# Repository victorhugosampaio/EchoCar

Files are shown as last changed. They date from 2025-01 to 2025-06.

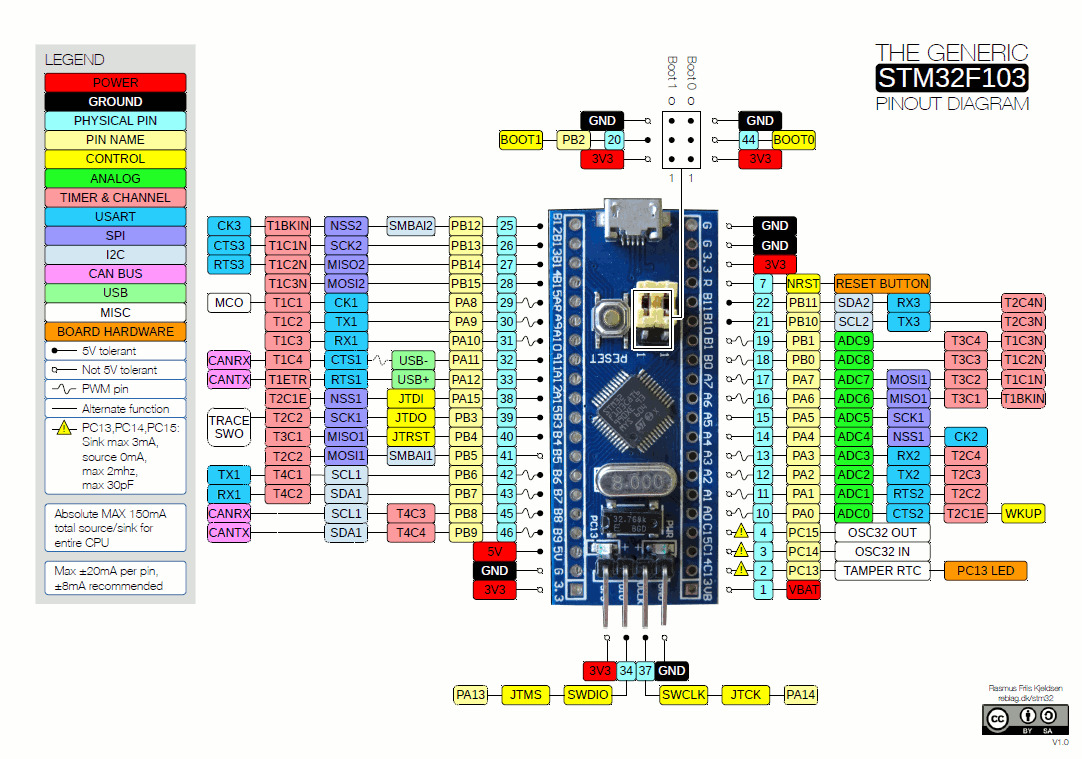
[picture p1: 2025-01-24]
images/Bluepill pinout.jpg

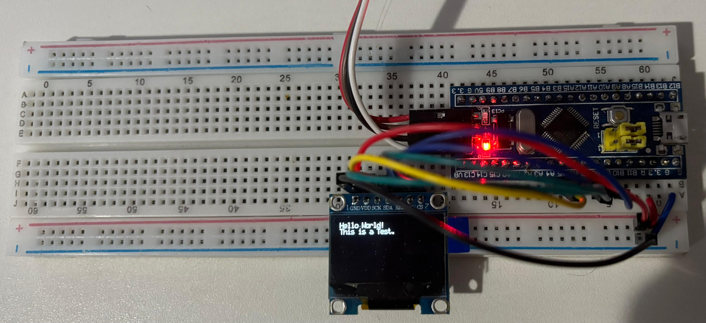
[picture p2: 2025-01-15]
images/display-test.jpg

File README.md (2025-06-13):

# EchoCar

Hi there, my name is Victor. I'm a ~~undergraduate~~ graduated computer engineer, currently working as a firmware trainee engineer. The EchoCar is my final paper project for college.

I used two microcontrollers: a Bluepill (STM32F103C8T6) to control the hardware itself and an Arduino Nano 33 BLE Sense to run the MFCC algorithm and the AI model. I chose to use Zephyr as the RTOS to operate the system. To create and train the AI model and deploy it to the Arduino Nano microcontroller, I used Edge Impulse. I also used it to edit some audio data to fit within the 1-second window for training the model.

I used the Pete Warden voice dataset as the AI databse. The files used in this project can be accessed [here](https://drive.google.com/file/d/17HAxpKHDkPuj7wIeOMZ8yrCH6MHIF1b3/view?usp=sharing).

## Getting Started

Follow these instructions to set up and run the EchoCar project.

### Prerequisites

The project is divided into firmware and hardware.

For the hardware, check the project BOM for the required components.

```
STM32F103C8T6 microcontroller  
Arduino Nano 33 BLE Sense  
EchoCar's PCB  
2x 18650 batteries  
BOM components  
```

For the firmware, install the Zephyr RTOS and the Arduino IDE. You can follow the instructions on the Zephyr Getting Started page to install it on your machine and download the Arduino IDE from their website.

### Installing

After installing Zephyr, flash the firmware onto the STM32F103 using a flasher device such as the ST-Link v2.

First, build the project using:

```
west build -p
```

Then, flash it using:

```
west flash
```

For the Arduino firmware, install the EchoCar_inferencing.rar library in the Arduino IDE, then flash the .ino file to the Arduino Nano microcontroller.

## Built With

* [Zephyr RTOS](https://www.zephyrproject.org/) - The RTOS used.  
* [Edge Impulse](https://edgeimpulse.com/) - Used for AI model development.  
* [KiCad](https://www.kicad.org/) - Used to design the PCB.
* [Pete Warden Dataset](https://arxiv.org/pdf/1804.03209) - AI Dataset.

## Author

* **Victor Hugo Sampaio**

## Video
YouTube [link](https://youtu.be/iiWRqvPNBO4).

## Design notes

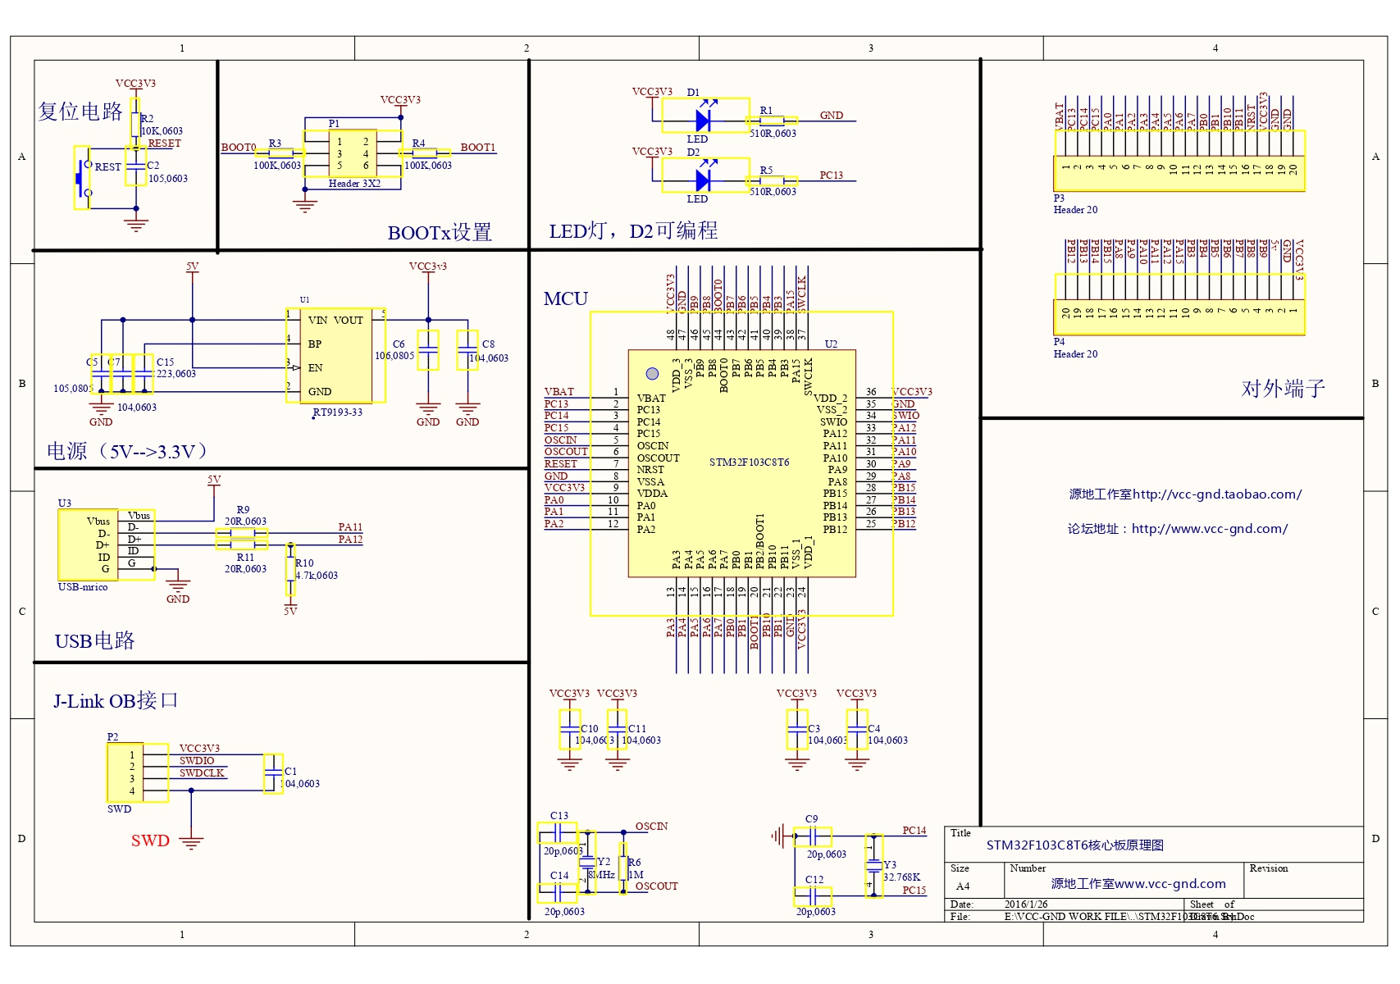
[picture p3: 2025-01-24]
images/Bluepill Schematic.jpg

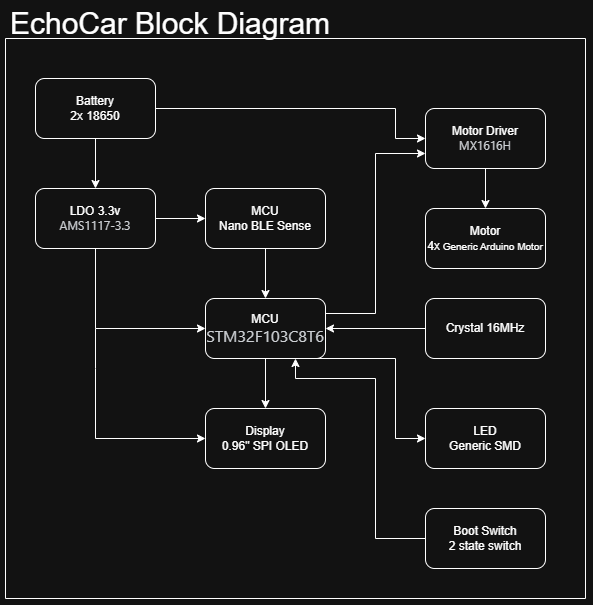
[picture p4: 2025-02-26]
images/EchoCar_Block_Diagram.png

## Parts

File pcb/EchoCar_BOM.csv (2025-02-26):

Reference | Value | Link | Footprint | Qty
C1 | 10u | https://www.lcsc.com/product-detail/Multilayer-Ceramic-Capacitors-MLCC-SMD-SMT_Murata-Electronics-GRM21BR61H106KE43L_C440198.html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 | Capacitor_SMD:C_0805_2012Metric | 1
C2,C3,C4,C5,C6,C7 | 100n | https://www.lcsc.com/product-detail/Multilayer-Ceramic-Capacitors-MLCC-SMD-SMT_TDK-C1005X7R1H104KT000F_C361198.html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 | Capacitor_SMD:C_0402_1005Metric | 6
C8,C9 | 10p | https://www.lcsc.com/product-detail/Multilayer-Ceramic-Capacitors-MLCC-SMD-SMT_TDK-CGA2B2NP01H100DT0Y0F_C694492.html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 | Capacitor_SMD:C_0402_1005Metric | 2
C10,C11 | 22u | https://www.lcsc.com/product-detail/Multilayer-Ceramic-Capacitors-MLCC-SMD-SMT_Samsung-Electro-Mechanics-CL21A226MAQNNNE_C45783.html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 | Capacitor_SMD:C_0805_2012Metric | 2
C12,C13 | 47u 16V | https://www.lcsc.com/product-detail/Aluminum-Electrolytic-Capacitors-SMD_AISHI-Aihua-Group-EMK1CM470E61D00R_C5289725.html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 | Capacitor_SMD:CP_Elec_5x5.3 | 2
D1 | PWR_ON | https://www.lcsc.com/product-detail/LED-Indication-Discrete_Foshan-NationStar-Optoelectronics-NCD0603W3_C158100.html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 | LED_SMD:LED_0603_1608Metric | 1
D2 | BZV55B5V1 | https://www.lcsc.com/product-detail/Zener-Diodes_EIC-Semicon-BZV55B5V1_C2978889.html?s_z=n_BZV55B5V1 | Diode_SMD:D_MiniMELF | 1
J1 | SW | x | Connector_PinHeader_2.54mm:PinHeader_1x04_P2.54mm_Vertical | 1
J2 | Display_Con | x | Connector_PinSocket_1.00mm:PinSocket_1x07_P2.54mm_Vertical | 1
J3 | Arduino_con | x | Connector_PinHeader_2.54mm:PinHeader_1x03_P2.54mm_Vertical | 1
R1 | 10k | https://www.lcsc.com/product-detail/Chip-Resistor-Surface-Mount_Vishay-Intertech-RCS040210K0FKED_C3020235.html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 | Resistor_SMD:R_0402_1005Metric | 1
R2 | 1k | https://www.lcsc.com/product-detail/Chip-Resistor-Surface-Mount_UNI-ROYAL-Uniroyal-Elec-CQ02WGJ0102TCE_C2770748.html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 | Resistor_SMD:R_0402_1005Metric | 1
R3 | 220 | https://www.lcsc.com/product-detail/Chip-Resistor-Surface-Mount_RALEC-RTT022200FTH_C102889.html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 | Resistor_SMD:R_0402_1005Metric | 1
SW1 | SW_SPDT | https://www.lcsc.com/product-detail/Slide-Switches_XKB-Connection-SK12D07L3B_C480339.html?s_z=n_SW%20SPDT | Button_Switch_THT:SW_E-Switch_EG1224_SPDT_Angled | 1
U1 | STM32F103C8T6 | https://www.lcsc.com/product-detail/Microcontrollers-MCU-MPU-SOC_STMicroelectronics-STM32F103C8T6_C8734.html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 | Package_QFP:LQFP-48_7x7mm_P0.5mm | 1
U2 | AMS1117-3.3 | https://www.lcsc.com/product-detail/Voltage-Regulators-Linear-Low-Drop-Out-LDO-Regulators_UMW-Youtai-Semiconductor-Co-Ltd-AMS1117-3-3_C347222.html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 | Package_TO_SOT_SMD:SOT-223-3_TabPin2 | 1
U3 | MX1616H | https://www.lcsc.com/product-detail/Brushed-DC-Motor-Drivers_Mixic-MX1616H_C5119044.html?s_z=n_MX1616H | MX1616H_SMD:MX1616H | 1
Y1 | 16MHz | https://www.lcsc.com/product-detail/Crystals_Shenzhen-SCTF-Elec-SX3B16-000F0910F30_C2901667.html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 | Crystal:Crystal_SMD_3225-4Pin_3.2x2.5mm | 1

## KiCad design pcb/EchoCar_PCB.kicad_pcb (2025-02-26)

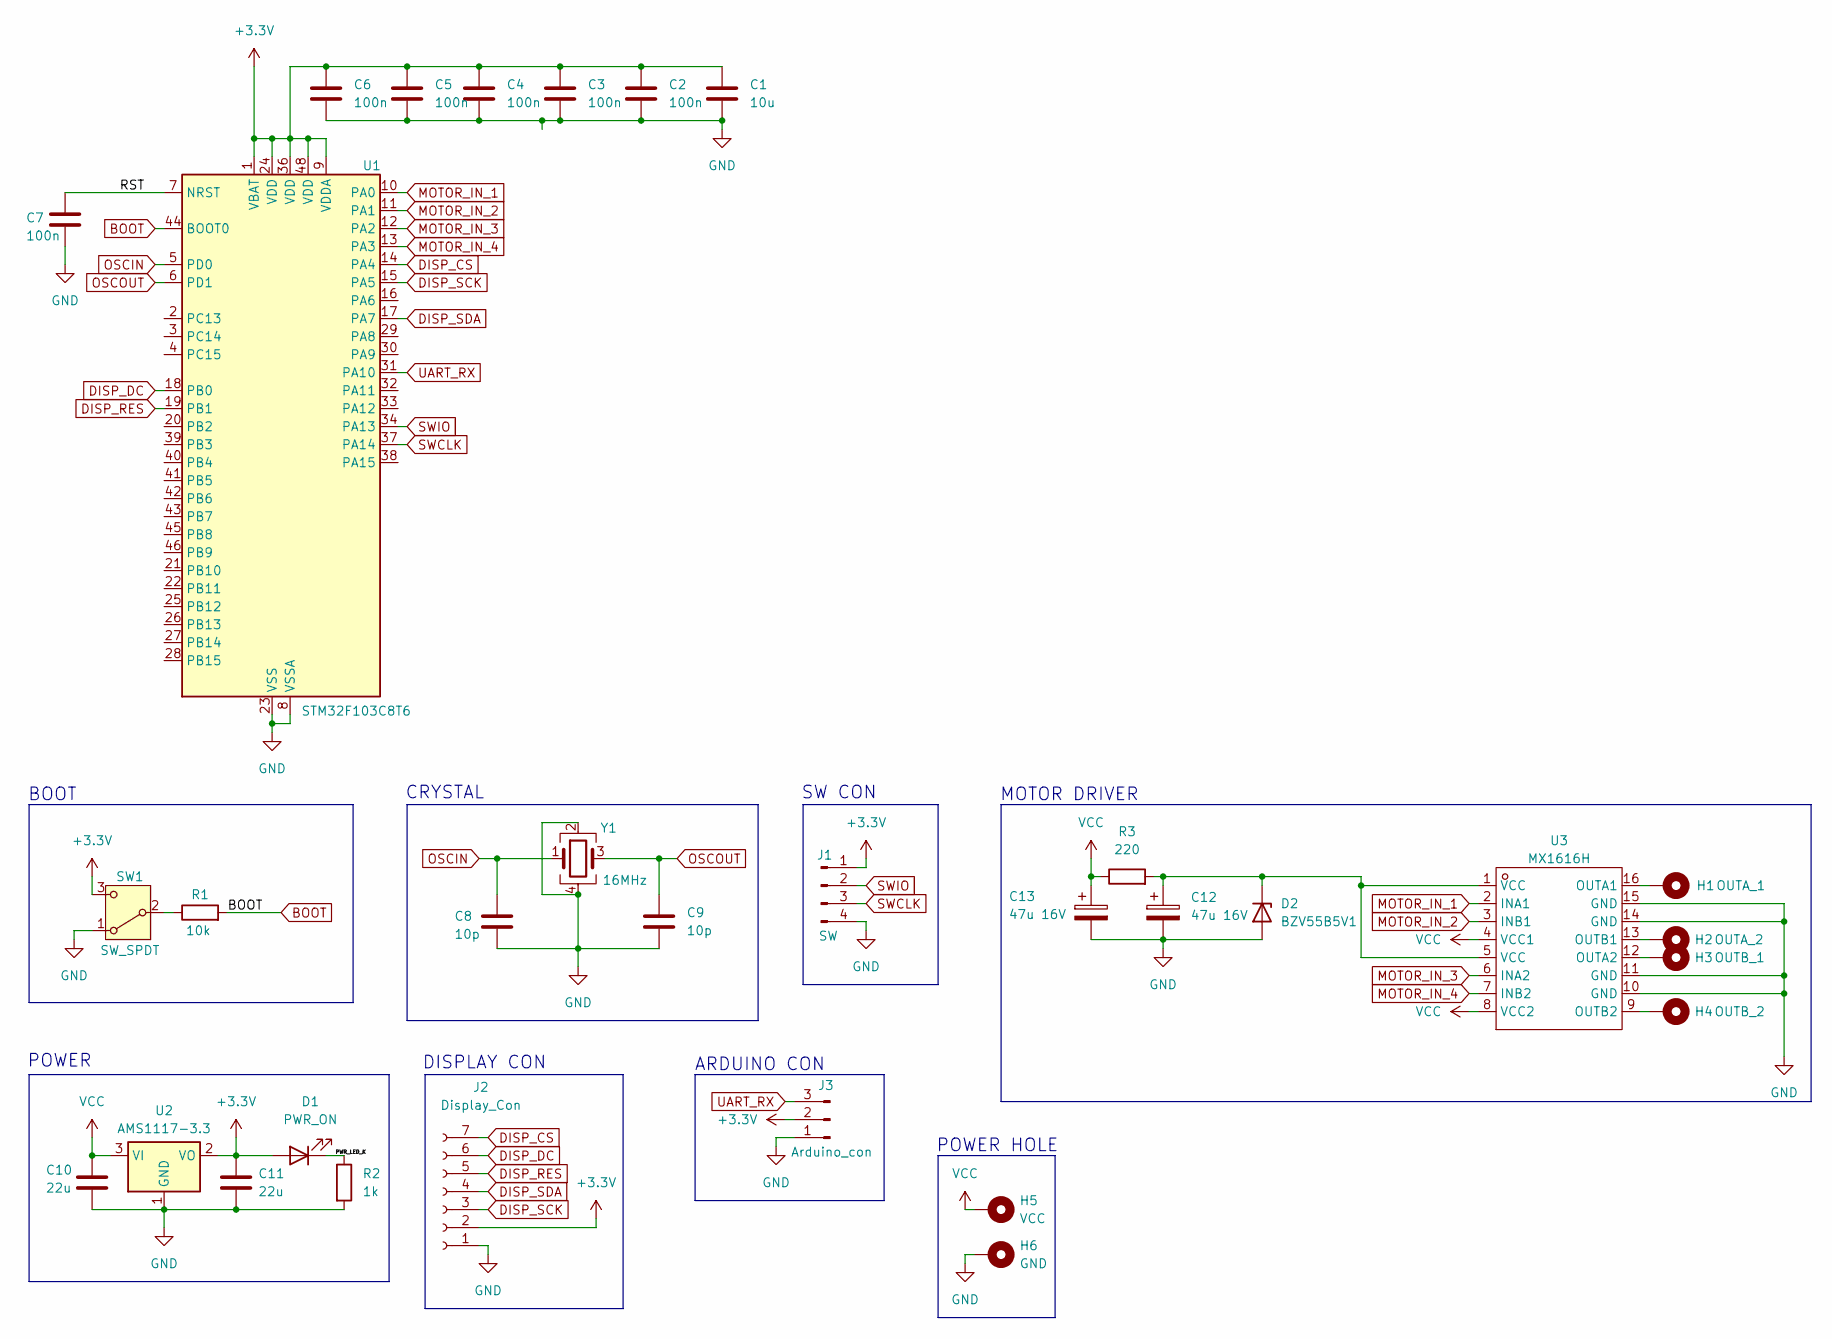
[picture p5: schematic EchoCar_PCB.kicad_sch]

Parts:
C1: 10u; C_0805_2012Metric
C2, C3, C4, C5, C6, C7: 100n; C_0402_1005Metric
C8, C9: 10p; C_0402_1005Metric
C10, C11: 22u; C_0805_2012Metric
C12, C13: 47u 16V; CP_Elec_5x5.3
D1: PWR_ON; LED_0603_1608Metric
D2: BZV55B5V1; D_MiniMELF
H1: OUTA_1; PinHeader_1x01_P2.54mm_Vertical
H2: OUTA_2; PinHeader_1x01_P2.54mm_Vertical
H3: OUTB_1; PinHeader_1x01_P2.54mm_Vertical
H4: OUTB_2; PinHeader_1x01_P2.54mm_Vertical
H5: VCC; PinHeader_1x01_P2.54mm_Vertical
H6: GND; PinHeader_1x01_P2.54mm_Vertical
J1: SW; PinHeader_1x04_P2.54mm_Vertical
J2: Display_Con; PinSocket_1x07_P2.54mm_Vertical
J3: Arduino_con; PinHeader_1x03_P2.54mm_Vertical
R1: 10k; R_0402_1005Metric
R2: 1k; R_0402_1005Metric
R3: 220; R_0402_1005Metric
SW1: SW_SPDT; SW_E-Switch_EG1224_SPDT_Angled
U1: STM32F103C8T6; LQFP-48_7x7mm_P0.5mm
U2: AMS1117-3.3; SOT-223-3_TabPin2
U3: MX1616H; LCSC Part Name MX1616H
Y1: 16MHz; Crystal_SMD_3225-4Pin_3.2x2.5mm

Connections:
+3.3V: C1.1, C2.1, C3.1, C4.1, C5.1, C6.1, C11.1, D1.2 (A), J1.1, J2.2, J3.2, SW1.3 (C), U1.1 (VBAT), U1.9 (VDDA), U1.24 (VDD), U1.36 (VDD), U1.48 (VDD), U2.2 (VO)
/PWR_LED_K: D1.1 (K), R2.1
/RST: C7.1, U1.7 (NRST)
BOOT: R1.2, U1.44 (BOOT0)
DISP_CS: J2.7, U1.14 (PA4)
DISP_DC: J2.6, U1.18 (PB0)
DISP_RES: J2.5, U1.19 (PB1)
DISP_SCK: J2.3, U1.15 (PA5)
DISP_SDA: J2.4, U1.17 (PA7)
GND: C1.2, C2.2, C3.2, C4.2, C5.2, C6.2, C7.2, C8.2, C9.2, C10.2, C11.2, C12.2, C13.2, D2.2 (A), H6.1, J1.4, J2.1, J3.1, R2.2, SW1.1 (A), U1.8 (VSSA), U1.23 (VSS), U1.35 (VSS), U1.47 (VSS), U2.1 (GND), U3.10 (GND), U3.11 (GND), U3.14 (GND), U3.15 (GND), Y1.2, Y1.4
MOTOR_IN_1: U1.10 (PA0), U3.2 (INA1)
MOTOR_IN_2: U1.11 (PA1), U3.3 (INB1)
MOTOR_IN_3: U1.12 (PA2), U3.6 (INA2)
MOTOR_IN_4: U1.13 (PA3), U3.7 (INB2)
unnamed: C12.1, D2.1 (K), R3.2, U3.1 (VCC), U3.5 (VCC)
unnamed: R1.1, SW1.2 (B)
unnamed: H1.1, U3.16 (OUTA1)
unnamed: H3.1, U3.12 (OUTA2)
unnamed: H2.1, U3.13 (OUTB1)
unnamed: H4.1, U3.9 (OUTB2)
OSCIN: C8.1, U1.5 (PD0), Y1.1
OSCOUT: C9.1, U1.6 (PD1), Y1.3
SWCLK: J1.3, U1.37 (PA14)
SWIO: J1.2, U1.34 (PA13)
UART_RX: J3.3, U1.31 (PA10)
VCC: C10.1, C13.1, H5.1, R3.1, U2.3 (VI), U3.4 (VCC1), U3.8 (VCC2)

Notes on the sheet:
ARDUINO CON
CRYSTAL
BOOT
POWER HOLE
POWER
MOTOR DRIVER
DISPLAY CON
SW CON

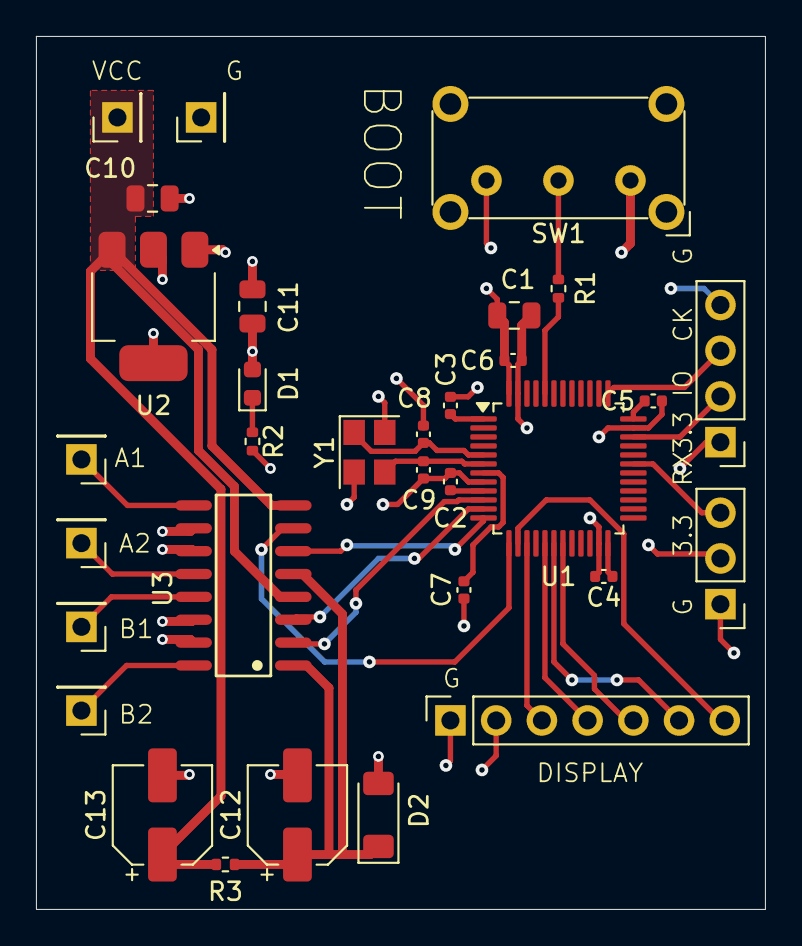
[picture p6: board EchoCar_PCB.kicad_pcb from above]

Board: 4 copper layers, 40.5 x 48.5 mm, 32 parts (0 on the bottom side), 26 nets.

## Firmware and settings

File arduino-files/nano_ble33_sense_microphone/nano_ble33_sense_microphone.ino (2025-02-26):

/* Edge Impulse ingestion SDK
 * Copyright (c) 2022 EdgeImpulse Inc.
 *
 * Licensed under the Apache License, Version 2.0 (the "License");
 * you may not use this file except in compliance with the License.
 * You may obtain a copy of the License at
 * http://www.apache.org/licenses/LICENSE-2.0
 *
 * Unless required by applicable law or agreed to in writing, software
 * distributed under the License is distributed on an "AS IS" BASIS,
 * WITHOUT WARRANTIES OR CONDITIONS OF ANY KIND, either express or implied.
 * See the License for the specific language governing permissions and
 * limitations under the License.
 *
 */

// If your target is limited in memory remove this macro to save 10K RAM
#define EIDSP_QUANTIZE_FILTERBANK 0

/* Includes ---------------------------------------------------------------- */
#include <PDM.h>
#include <EchoCar_inferencing.h>

/** Audio buffers, pointers and selectors */
typedef struct {
  int16_t *buffer;
  uint8_t buf_ready;
  uint32_t buf_count;
  uint32_t n_samples;
} inference_t;

static inference_t inference;
static signed short sampleBuffer[2048];
static bool debug_nn = false;  // Set this to true to see e.g. features generated from the raw signal

/* EchoCar Variables */
enum predictions {
  BACKWARD,
  FIVE,
  FORWARD,
  FOUR,
  GO,
  LEFT,
  NOISE,
  ONE,
  RIGHT,
  STOP,
  THREE,
  TWO,
};

static size_t highest_value = 0;
static size_t highest_prediction = NOISE;

void setup() {
  Serial.begin(115200);
  Serial1.begin(115200);

  Serial.println("Edge Impulse Inferencing Demo");

  // summary of inferencing settings (from model_metadata.h)
  ei_printf("Inferencing settings:\n");
  ei_printf("\tInterval: %.2f ms.\n", (float)EI_CLASSIFIER_INTERVAL_MS);
  ei_printf("\tFrame size: %d\n", EI_CLASSIFIER_DSP_INPUT_FRAME_SIZE);
  ei_printf("\tSample length: %d ms.\n", EI_CLASSIFIER_RAW_SAMPLE_COUNT / 16);
  ei_printf("\tNo. of classes: %d\n", sizeof(ei_classifier_inferencing_categories) / sizeof(ei_classifier_inferencing_categories[0]));

  if (microphone_inference_start(EI_CLASSIFIER_RAW_SAMPLE_COUNT) == false) {
    ei_printf("ERR: Could not allocate audio buffer (size %d), this could be due to the window length of your model\r\n", EI_CLASSIFIER_RAW_SAMPLE_COUNT);
    return;
  }
}

void loop() {
  ei_printf("Recording...\n");

  bool m = microphone_inference_record();
  if (!m) {
    ei_printf("ERR: Failed to record audio...\n");
    return;
  }

  ei_printf("Recording done\n");

  signal_t signal;
  signal.total_length = EI_CLASSIFIER_RAW_SAMPLE_COUNT;
  signal.get_data = &microphone_audio_signal_get_data;
  ei_impulse_result_t result = { 0 };

  EI_IMPULSE_ERROR r = run_classifier(&signal, &result, debug_nn);
  if (r != EI_IMPULSE_OK) {
    ei_printf("ERR: Failed to run classifier (%d)\n", r);
    return;
  }

  ei_printf("Predictions ");
  ei_printf("(DSP: %d ms., Classification: %d ms., Anomaly: %d ms.)",
            result.timing.dsp, result.timing.classification, result.timing.anomaly);
  ei_printf(": \n");
  for (size_t ix = 0; ix < EI_CLASSIFIER_LABEL_COUNT; ix++) {
    ei_printf("    %s: %.5f\n", result.classification[ix].label, result.classification[ix].value);
    result.classification[ix].value = result.classification[ix].value * 100;

    if (result.classification[ix].value > highest_value) {
      highest_value = result.classification[ix].value;
      highest_prediction = ix;
    }
  }

  Serial1.write(highest_prediction + 'a'); /* Send highest prediction via UART. */
  Serial.print("Sent: ");
  Serial.println(highest_prediction);

  highest_value = 0;

  delay(100); /* UART delay. */
}

/**
 * @brief      PDM buffer full callback
 *             Get data and call audio thread callback
 */
static void pdm_data_ready_inference_callback(void) {
  int bytesAvailable = PDM.available();

  // read into the sample buffer
  int bytesRead = PDM.read((char *)&sampleBuffer[0], bytesAvailable);

  if (inference.buf_ready == 0) {
    for (int i = 0; i < bytesRead >> 1; i++) {
      inference.buffer[inference.buf_count++] = sampleBuffer[i];

      if (inference.buf_count >= inference.n_samples) {
        inference.buf_count = 0;
        inference.buf_ready = 1;
        break;
      }
    }
  }
}

/**
 * @brief      Init inferencing struct and setup/start PDM
 *
 * @param[in]  n_samples  The n samples
 *
 * @return     { description_of_the_return_value }
 */
static bool microphone_inference_start(uint32_t n_samples) {
  inference.buffer = (int16_t *)malloc(n_samples * sizeof(int16_t));

  if (inference.buffer == NULL) {
    return false;
  }

  inference.buf_count = 0;
  inference.n_samples = n_samples;
  inference.buf_ready = 0;

  // configure the data receive callback
  PDM.onReceive(&pdm_data_ready_inference_callback);

  PDM.setBufferSize(4096);

  // initialize PDM with:
  // - one channel (mono mode)
  // - a 16 kHz sample rate
  if (!PDM.begin(1, EI_CLASSIFIER_FREQUENCY)) {
    ei_printf("Failed to start PDM!");
    microphone_inference_end();

    return false;
  }

  // set the gain, defaults to 20
  PDM.setGain(127);

  return true;
}

/**
 * @brief      Wait on new data
 *
 * @return     True when finished
 */
static bool microphone_inference_record(void) {
  inference.buf_ready = 0;
  inference.buf_count = 0;

  while (inference.buf_ready == 0) {
    delay(10);
  }

  return true;
}

/**
 * Get raw audio signal data
 */
static int microphone_audio_signal_get_data(size_t offset, size_t length, float *out_ptr) {
  numpy::int16_to_float(&inference.buffer[offset], out_ptr, length);

  return 0;
}

/**
 * @brief      Stop PDM and release buffers
 */
static void microphone_inference_end(void) {
  PDM.end();
  free(inference.buffer);
}

#if !defined(EI_CLASSIFIER_SENSOR) || EI_CLASSIFIER_SENSOR != EI_CLASSIFIER_SENSOR_MICROPHONE
#error "Invalid model for current sensor."
#endif

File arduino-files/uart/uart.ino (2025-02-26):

enum prediction {
    PREDICTION_BACKWARD,
    PREDICTION_FIVE,
    PREDICTION_FORWARD,
    PREDICTION_FOUR,
    PREDICTION_GO,
    PREDICTION_LEFT,
    PREDICTION_NOISE,
    PREDICTION_ONE,
    PREDICTION_RIGHT,
    PREDICTION_STOP,
    PREDICTION_THREE,
    PREDICTION_TWO,

    PREDICTION_QUANTITY,
};

const unsigned char chars[PREDICTION_QUANTITY] = {
    [PREDICTION_BACKWARD] = 'a',
    [PREDICTION_FIVE] = 'b',
    [PREDICTION_FORWARD] = 'c',
    [PREDICTION_FOUR] = 'd',
    [PREDICTION_GO] = 'e',
    [PREDICTION_LEFT] = 'f',
    [PREDICTION_NOISE] = 'g',
    [PREDICTION_ONE] = 'h',
    [PREDICTION_RIGHT] = 'i',
    [PREDICTION_STOP] = 'j',
    [PREDICTION_THREE] = 'k',
    [PREDICTION_TWO] = 'l',
  };

unsigned long previousMillis = 0;
const long interval = 3000; // 3 segundos

void setup() {
    Serial.begin(9600);
    Serial1.begin(115200);
}

void loop() {
    unsigned long currentMillis = millis();

    if (currentMillis - previousMillis >= interval) {
        previousMillis = currentMillis;

        static int index = 0;
        Serial.println(chars[index]); // Print no Serial normal
        Serial1.write(chars[index]); // Envio via Serial1

        index++;
        if (index >= 12) {
            index = 0;
        }
    }

    delay(100); // Necessário para a UART
}

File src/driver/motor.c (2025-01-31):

/**
 * @file motor.c
 * @author victorhugosampaio
 * @brief L293D motor driver.
 * @version 0.1
 * @date 01-21-2025
 *
 * @note: Based on https://www.instructables.com/Tutorial-for-Dual-Channel-DC-Motor-Driver-Board-PW/
 *
 * @copyright Copyright (c) 2025
 *
 */

#include "motor.h"

#include <errno.h>
#include <zephyr/device.h>
#include <zephyr/drivers/pwm.h>
#include <zephyr/kernel.h>
#include <zephyr/logging/log.h>

LOG_MODULE_REGISTER(motor);

/**
 * @brief Container that holds the PWM devices.
 */
static const struct pwm_dt_spec in_1 = PWM_DT_SPEC_GET_BY_NAME(DT_PATH(zephyr_user), in_1);
static const struct pwm_dt_spec in_2 = PWM_DT_SPEC_GET_BY_NAME(DT_PATH(zephyr_user), in_2);
static const struct pwm_dt_spec in_3 = PWM_DT_SPEC_GET_BY_NAME(DT_PATH(zephyr_user), in_3);
static const struct pwm_dt_spec in_4 = PWM_DT_SPEC_GET_BY_NAME(DT_PATH(zephyr_user), in_4);

int motor_init(void)
{
    if (!pwm_is_ready_dt(&in_1) || !pwm_is_ready_dt(&in_2) || !pwm_is_ready_dt(&in_3) || !pwm_is_ready_dt(&in_4)) {
        LOG_ERR("motor is not ready");
        return -EBUSY;
    }

    motor_input_set(IN_1, 0);
    motor_input_set(IN_2, 0);
    motor_input_set(IN_3, 0);
    motor_input_set(IN_4, 0);

    return 0;
}

void motor_input_set(const enum motor_input input, const bool value)
{
    uint16_t pulse = 0;

    switch (input) {
    case IN_1:
        pulse = value ? CONFIG_IN_1_MAX_PULSE : CONFIG_IN_1_MIN_PULSE;
        pwm_set_pulse_dt(&in_1, pulse);
        break;
    case IN_2:
        pulse = value ? CONFIG_IN_2_MAX_PULSE : CONFIG_IN_2_MIN_PULSE;
        pwm_set_pulse_dt(&in_2, pulse);
        break;
    case IN_3:
        pulse = value ? CONFIG_IN_3_MAX_PULSE : CONFIG_IN_3_MIN_PULSE;
        pwm_set_pulse_dt(&in_3, pulse);
        break;
    case IN_4:
        pulse = value ? CONFIG_IN_4_MAX_PULSE : CONFIG_IN_4_MIN_PULSE;
        pwm_set_pulse_dt(&in_4, pulse);
        break;
    default:
        break;
    }
}

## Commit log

2025-01-15 feat: Create the display driver.
    Create the display driver for the SPI 0.96'' OLED Display with the SSD1306 driver.
2025-01-21 refactor: Refactor the display driver.
    Change the 5x7 font to the 8x8 and adjust some code lines.
2025-01-21 feat: Create the motor driver.
    Create the motor driver for the L293D H driver.
2025-01-23 refactor: Finish the car handler.
    Adjust the motor driver and finish the car handler.
2025-01-23 fix: Fix changes.
    Fix name changes.
    [motor.c]
2025-01-23 fix: Overlay fix.
    Fix the board overlay file.
2025-01-24 feat: Create the usart driver.
    Create the usart driver and adapt the car handler.
2025-01-24 fix: Fix the usart driver.
    Fix the usart driver.
    [car_handler.c, main.c, usart.c]
2025-01-27 fix: Fix usart.
    Fix some usart bugs due to some default configurations.
    [car_handler.c, motor.c, usart.c]
2025-02-11 feat: Create the PCB.
    Create the car pcb.
    [EchoCar_PCB.kicad_pcb, EchoCar_PCB.kicad_sch]
2025-02-17 feat: Add the MX1616H.
    Create the MX1616H footprint and symbol.
2025-02-17 feat: Add the motor driver.
    Add the motor driver to the schematic.
    [EchoCar_PCB.kicad_sch]
2025-02-20 feat: Conclude the schematic.
    Conclude the pcb schematic and add the BOM.
    [EchoCar_BOM.csv, EchoCar_PCB.kicad_sch]
2025-02-26 feat: Finish the PCB.
    Finish the project PCB.
    [EchoCar_PCB-3V3_Cu.gbr, EchoCar_PCB-B_Cu.gbr, EchoCar_PCB-B_Mask.gbr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]
2025-02-26 feat: Add the arduino files.
    Add the Nano BLE Sense files (UART and the ML model).
2025-02-26 Create the block diagram.
    Create the EchoCar PCB block diagram.
2025-03-19 feat: add the used scripts.
    Add the script used to select random samples.
2025-05-13 fix: fix car handler
    Fix time displaying on car handler.
    [car_handler.c]
